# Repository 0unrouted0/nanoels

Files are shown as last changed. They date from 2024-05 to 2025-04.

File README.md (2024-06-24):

This software and instructions are [provided as is](LICENSE), without warranty of any kind.

See [the data of kachurovskiy](https://github.com/kachurovskiy/nanoels/) for the original NanoEls

# NanoEls H4 revised1 (currently unfinished work!!)
* This is an idea of an low cost variant with multiple placement and handsolder types for the components. For e.g.
    * PCB double sided 100mm x 100mm standard type
    * Design with free KiCad 8
    * All parts for hand solder (TCA8418 tricky, but possible - or usage of Adafruit Module)
    * One PCB for keypad and controls
    * Powering over USB or step-down converter with screw terminals
    * Interfacing to LCD via I2C interface over 4 pins possible (== same LCD type with I2C backpack PCB as sold on Aliexpress)
    * USB program and serial interface variants FT232RL or CH340 series
    * USB Connectors 90° types in two sides (idea: back connector>power, front connector>PC-control) or side entry both over 180° Types
    * ESP32-S3-WROOM-1 also possible (with antenna), currently used N16R8

* What's working in Hardware (with modified software)?
	* WARNING: This special hardware version is not checked against EMC, CE, FCC and so on...
    * Display over I2C Interface
    * Programming and serial interface over FT232RL for the ESP32-S3-WROOM-1 (N16R8)
    * Keypad with direct soldered Keypad controller

* What's working in Software?
    * Software should be (i can not test it) compatible with the original NanoEls H4
    * Software working with ardunio Espressive ESP32 3.0.1 boards package (based on ESP-IDF v5.1.4). Maybe NOT backwards compatible to 2.x.
    * Display in I2C mode working. Faultless together with secondary I2C channel for keypad interface. 
    * Added LiquidCrystal_I2C_pt for handling of two I2C interfaces an changeable pins, because there are no available Arduino libraries with I2C pointer parameter.
    * Currently not completely tested, but encoder detects something. Hardware timer for ASYNC and A1 mode maybe not 100% working (unclear).

* ToDo's and current bugs
    * More testing of HW and SW
    * Integration in a real lathe
    * Making a low cost 3d-printable housing
    * PCB: Pitch of buzzer is false for the delivered type. Maybe a dual pitch package is sensible
    * PCB: Through hole pad for thermal connection of ESP32 module should have a bigger size free of solder mask
    * PCB: maybe dual package in standard sizes for buzzer free wheeling diode
    * PCB: upload the latest version

PCB_H4revised1_3d_viewer
PCB_H4revised1_pic1

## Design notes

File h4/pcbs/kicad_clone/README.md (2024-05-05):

- imported easyeda projects directly with KiCad 8.0.2 and saved files
- seems OK, but not tested for importing failures

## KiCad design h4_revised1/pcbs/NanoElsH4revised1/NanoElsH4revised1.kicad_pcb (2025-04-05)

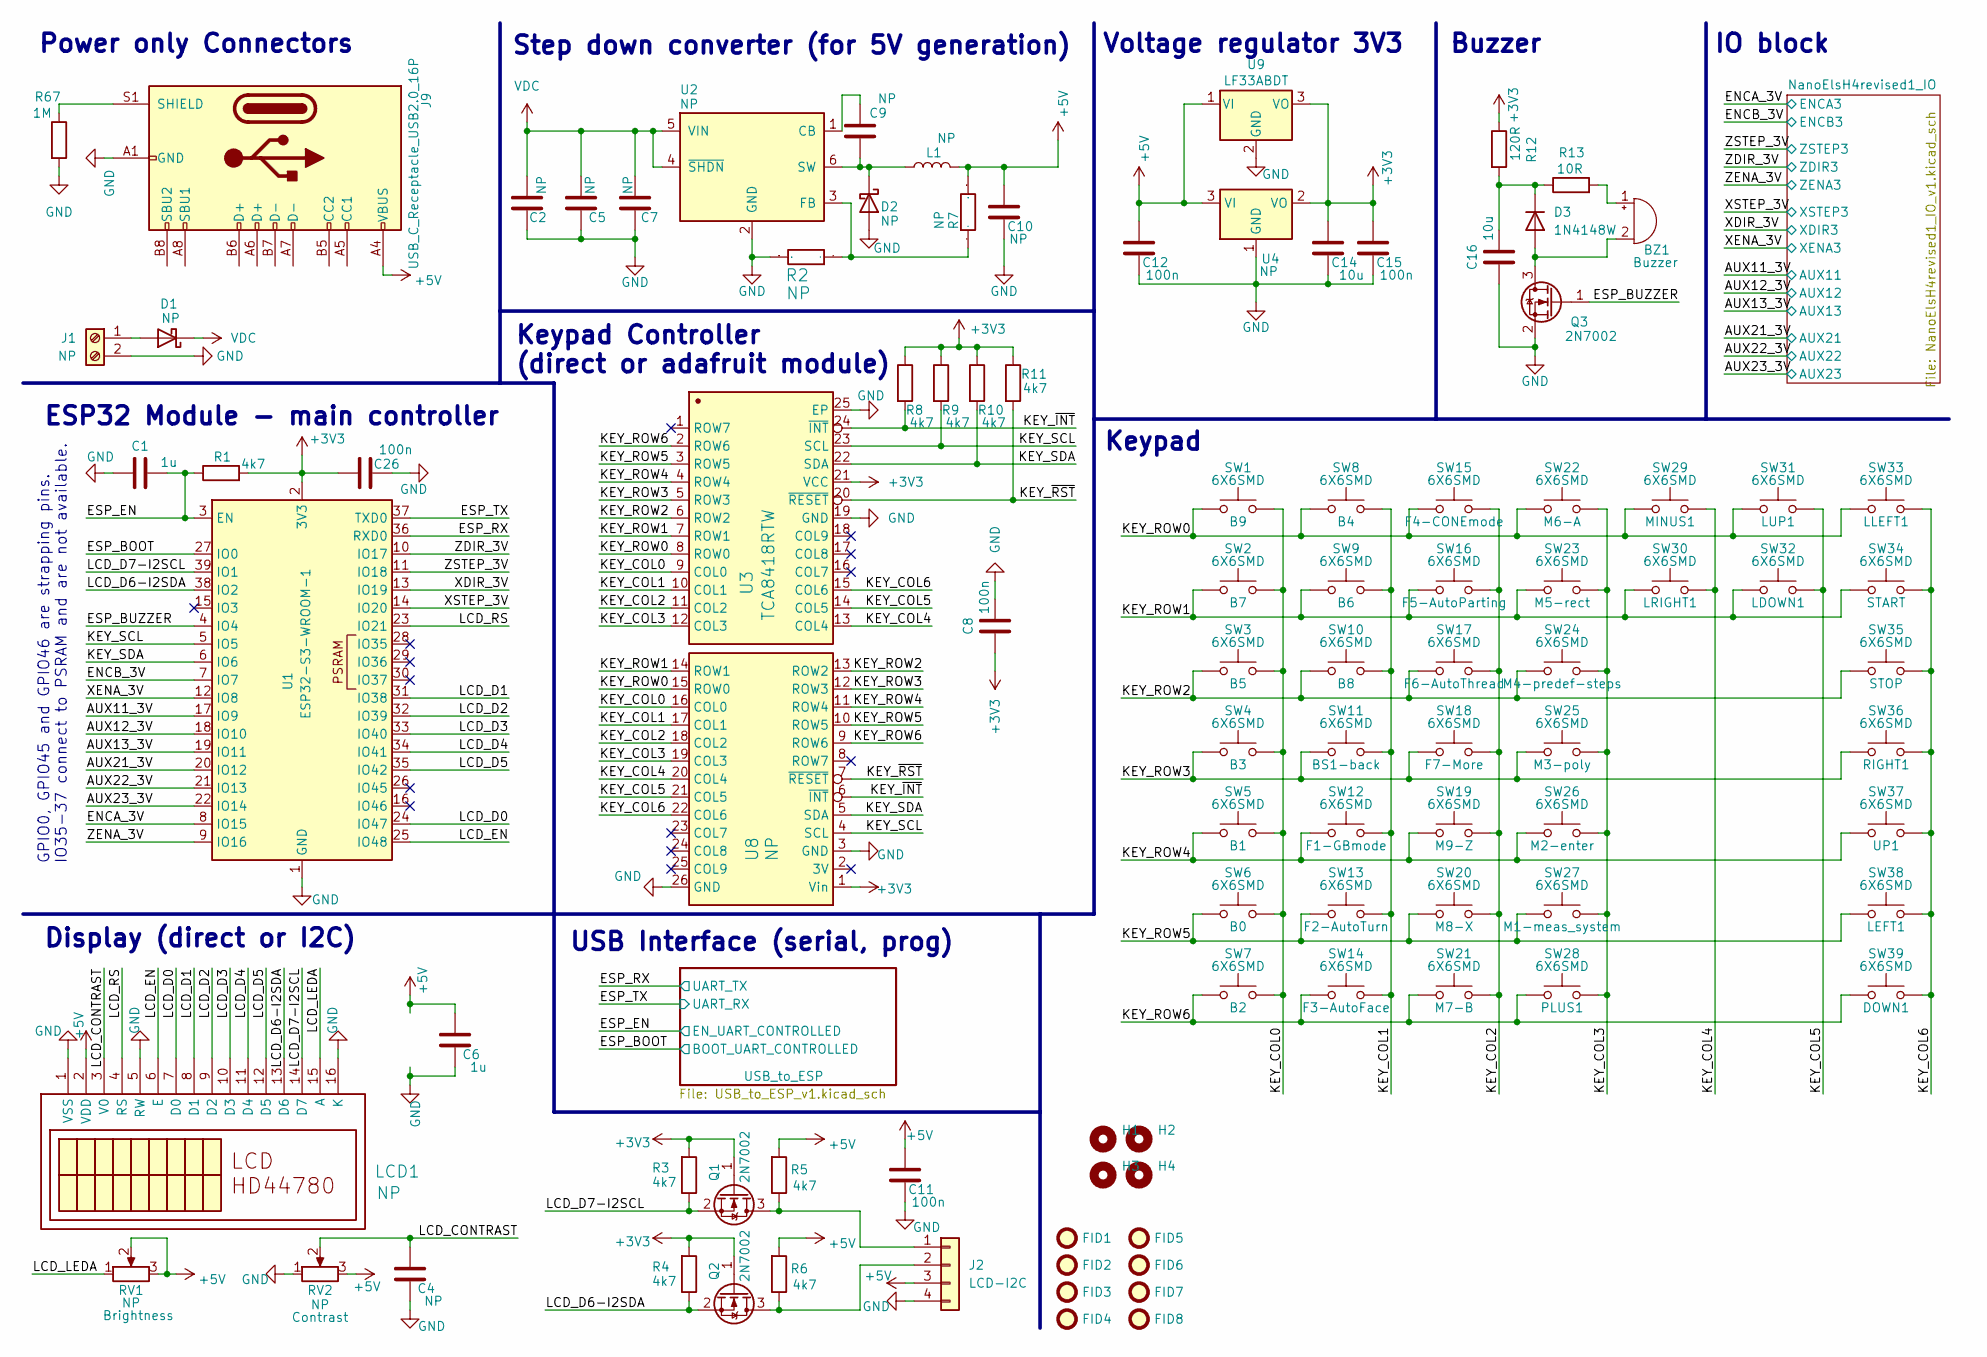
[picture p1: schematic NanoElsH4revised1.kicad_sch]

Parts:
BZ1: Buzzer; MagneticBuzzer_PUI_AT-0927-TT-6-R
C1, C6: 1u; C_0603_1608Metric
C2, C5: NP; C_1210_3225Metric
C4, C7, C9: NP; C_0603_1608Metric
C8, C11, C12, C15, C26: 100n; C_0603_1608Metric
C10: NP; C_1206_3216Metric
C14, C16: 10u; C_1206_3216Metric
D1, D2: NP; D_SMA
D3: 1N4148W; D_SOD-323
FID1, FID2, FID3, FID4, FID5, FID6, FID7, FID8: Fiducial_1.5mm_Mask3mm
H1, H2, H3, H4: MountingHole_3.2mm_M3
J1: NP; PhoenixContact_MCV_1,5_2-G-3.5_1x02_P3.50mm_Vertical
J2: LCD-I2C; PinHeader_1x04_P2.54mm_Horizontal
J9: USB_C_Receptacle_USB2.0_16P; USB_C_HorVert_topbot_GCT-JAE-HRO_USB4160-DX07S024WJ3R400-C3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
L1: NP; L_TDK_VLS6045EX_VLS6045AF
LCD1: NP; LCD_HD44780_header_horizontal
Q1, Q2, Q3: 2N7002; SOT-23
R1, R3, R4, R5, R6, R8, R9, R10, R11: 4k7; R_0603_1608Metric
R2, R7: NP; R_0603_1608Metric
R12: 120R; R_0603_1608Metric
R13: 10R; R_0603_1608Metric
R67: 1M; R_0603_1608Metric
RV1, RV2: NP; Potentiometer_ACP_CA6-VSMD_Vertical
SW1, SW2, SW3, SW4, SW5, SW6, SW7, SW8, SW9, SW10, SW11, SW12, SW13, SW14, SW15, SW16, SW17, SW18, SW19, SW20, SW21, SW22, SW23, SW24, SW25, SW26, SW27, SW28, SW29, SW30, SW31, SW32, SW33, SW34, SW35, SW36, SW37, SW38, SW39: 6X6SMD; SW_Push_1P1T_NO_6x6mm_H9.5mm
U1: ESP32-S3-WROOM-1; ESP32-S3-WROOM-1_bighole
U2: NP; SOT-23-6
U3: TCA8418RTW; WQFN-24-1EP_4x4mm_P0.5mm_EP2.45x2.45mm
U4: NP; SOT-223-3_TabPin2
U8: NP; Adafruit_STEMMA_TCA8418
U9: LF33ABDT; TO-252-2

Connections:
+3V3: C8.1, C14.2, C15.2, C26.2, Q1.1 (G), Q2.1 (G), R1.2, R3.2, R4.2, R8.1, R9.1, R10.1, R11.1, R12.1, U1.2 (3V3), U3.21 (VCC), U4.2 (VO), U8.1 (Vin), U9.3 (VO); also elsewhere on the board
+5V: C6.2, C10.2, C11.2, C12.2, J2.3, J9.A4 (VBUS), J9.A9 (VBUS), J9.B4 (VBUS), J9.B9 (VBUS), L1.2, LCD1.2 (VDD), R5.2, R6.2, R7.1, RV1.2, RV1.3, RV2.3, U4.3 (VI), U9.1 (VI); also elsewhere on the board
/AUX11_3V: U1.17 (IO9); also elsewhere on the board
/AUX12_3V: U1.18 (IO10); also elsewhere on the board
/AUX13_3V: U1.19 (IO11); also elsewhere on the board
/AUX21_3V: U1.20 (IO12); also elsewhere on the board
/AUX22_3V: U1.21 (IO13); also elsewhere on the board
/AUX23_3V: U1.22 (IO14); also elsewhere on the board
/ENCA_3V: U1.8 (IO15); also elsewhere on the board
/ENCB_3V: U1.7 (IO7); also elsewhere on the board
/ESP_BOOT: U1.27 (IO0); also elsewhere on the board
/ESP_BUZZER: Q3.1 (G), U1.4 (IO4)
/ESP_EN: C1.2, R1.1, U1.3 (EN); also elsewhere on the board
/ESP_RX: U1.36 (RXD0); also elsewhere on the board
/ESP_TX: U1.37 (TXD0); also elsewhere on the board
/KEY_COL0: SW1.2, SW2.2, SW3.2, SW4.2, SW5.2, SW6.2, SW7.2, U3.9 (COL0), U8.16 (COL0)
/KEY_COL1: SW8.2, SW9.2, SW10.2, SW11.2, SW12.2, SW13.2, SW14.2, U3.10 (COL1), U8.17 (COL1)
/KEY_COL2: SW15.2, SW16.2, SW17.2, SW18.2, SW19.2, SW20.2, SW21.2, U3.11 (COL2), U8.18 (COL2)
/KEY_COL3: SW22.2, SW23.2, SW24.2, SW25.2, SW26.2, SW27.2, SW28.2, U3.12 (COL3), U8.19 (COL3)
/KEY_COL4: SW29.2, SW30.2, U3.13 (COL4), U8.20 (COL4)
/KEY_COL5: SW31.2, SW32.2, U3.14 (COL5), U8.21 (COL5)
/KEY_COL6: SW33.2, SW34.2, SW35.2, SW36.2, SW37.2, SW38.2, SW39.2, U3.15 (COL6), U8.22 (COL6)
/KEY_ROW0: SW1.1, SW8.1, SW15.1, SW22.1, SW29.1, SW31.1, SW33.1, U3.8 (ROW0), U8.15 (ROW0)
/KEY_ROW1: SW2.1, SW9.1, SW16.1, SW23.1, SW30.1, SW32.1, SW34.1, U3.7 (ROW1), U8.14 (ROW1)
/KEY_ROW2: SW3.1, SW10.1, SW17.1, SW24.1, SW35.1, U3.6 (ROW2), U8.13 (ROW2)
/KEY_ROW3: SW4.1, SW11.1, SW18.1, SW25.1, SW36.1, U3.5 (ROW3), U8.12 (ROW3)
/KEY_ROW4: SW5.1, SW12.1, SW19.1, SW26.1, SW37.1, U3.4 (ROW4), U8.11 (ROW4)
/KEY_ROW5: SW6.1, SW13.1, SW20.1, SW27.1, SW38.1, U3.3 (ROW5), U8.10 (ROW5)
/KEY_ROW6: SW7.1, SW14.1, SW21.1, SW28.1, SW39.1, U3.2 (ROW6), U8.9 (ROW6)
/KEY_SCL: R9.2, U1.5 (IO5), U3.23 (SCL), U8.4 (SCL)
/KEY_SDA: R10.2, U1.6 (IO6), U3.22 (SDA), U8.5 (SDA)
/KEY_~INT: R8.2, U3.24 (~INT), U8.6 (~INT)
/KEY_~RST: R11.2, U3.20 (~RESET), U8.7 (~RESET)
/LCD_CONTRAST: C4.2, LCD1.3 (V0), RV2.2
/LCD_D0: LCD1.7 (D0), U1.24 (IO47)
/LCD_D1: LCD1.8 (D1), U1.31 (IO38)
/LCD_D2: LCD1.9 (D2), U1.32 (IO39)
/LCD_D3: LCD1.10 (D3), U1.33 (IO40)
/LCD_D4: LCD1.11 (D4), U1.34 (IO41)
/LCD_D5: LCD1.12 (D5), U1.35 (IO42)
/LCD_D6-I2SDA: LCD1.13 (D6), Q2.2 (S), R4.1, U1.38 (IO2)
/LCD_D7-I2SCL: LCD1.14 (D7), Q1.2 (S), R3.1, U1.39 (IO1)
/LCD_EN: LCD1.6 (E), U1.25 (IO48)
/LCD_LEDA: LCD1.15 (A), RV1.1
/LCD_RS: LCD1.4 (RS), U1.23 (IO21)
/XDIR_3V: U1.13 (IO19); also elsewhere on the board
/XENA_3V: U1.12 (IO8); also elsewhere on the board
/XSTEP_3V: U1.14 (IO20); also elsewhere on the board
/ZDIR_3V: U1.10 (IO17); also elsewhere on the board
/ZENA_3V: U1.9 (IO16); also elsewhere on the board
/ZSTEP_3V: U1.11 (IO18); also elsewhere on the board
GND: C1.1, C2.1, C4.1, C5.1, C6.1, C7.1, C8.2, C10.1, C11.1, C12.1, C14.1, C15.1, C16.1, C26.1, D2.2 (A), J1.2, J2.4, J9.A1 (GND), J9.A12 (GND), J9.B1 (GND), J9.B12 (GND), LCD1.1 (VSS), LCD1.5 (RW), LCD1.16 (K), Q3.2 (S), R2.1, R67.2, RV2.1, U1.1 (GND), U1.40 (GND), U1.41 (GND), U2.2 (GND), U3.19 (GND), U3.25 (EP), U4.1 (GND), U8.3 (GND), U8.26 (GND), U9.2 (GND); also elsewhere on the board
unnamed: BZ1.1 (+), R13.2
unnamed: BZ1.2 (-), D3.2 (A), Q3.3 (D)
unnamed: D1.2 (A), J1.1
unnamed: C9.1, D2.1 (K), L1.1, U2.6 (SW)
unnamed: C16.2, D3.1 (K), R12.2, R13.1
unnamed: J2.1, Q1.3 (D), R5.1
unnamed: J2.2, Q2.3 (D), R6.1
unnamed: J9.S1 (SHIELD), R67.1
unnamed: C9.2, U2.1 (CB)
unnamed: R2.2, R7.2, U2.3 (FB)
VDC: C2.2, C5.2, C7.2, D1.1 (K), U2.4 (~SHDN), U2.5 (VIN)

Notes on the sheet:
USB Interface (serial, prog)
Step down converter (for 5V generation)
Keypad Controller (direct or adafruit module)
GPIO0, GPIO45 and GPIO46 are strapping pins. IO35-37 connect to PSRAM and are not available.
Keypad
ESP32 Module - main controller
Power only Connectors
Buzzer
Display (direct or I2C)
Voltage regulator 3V3
IO block

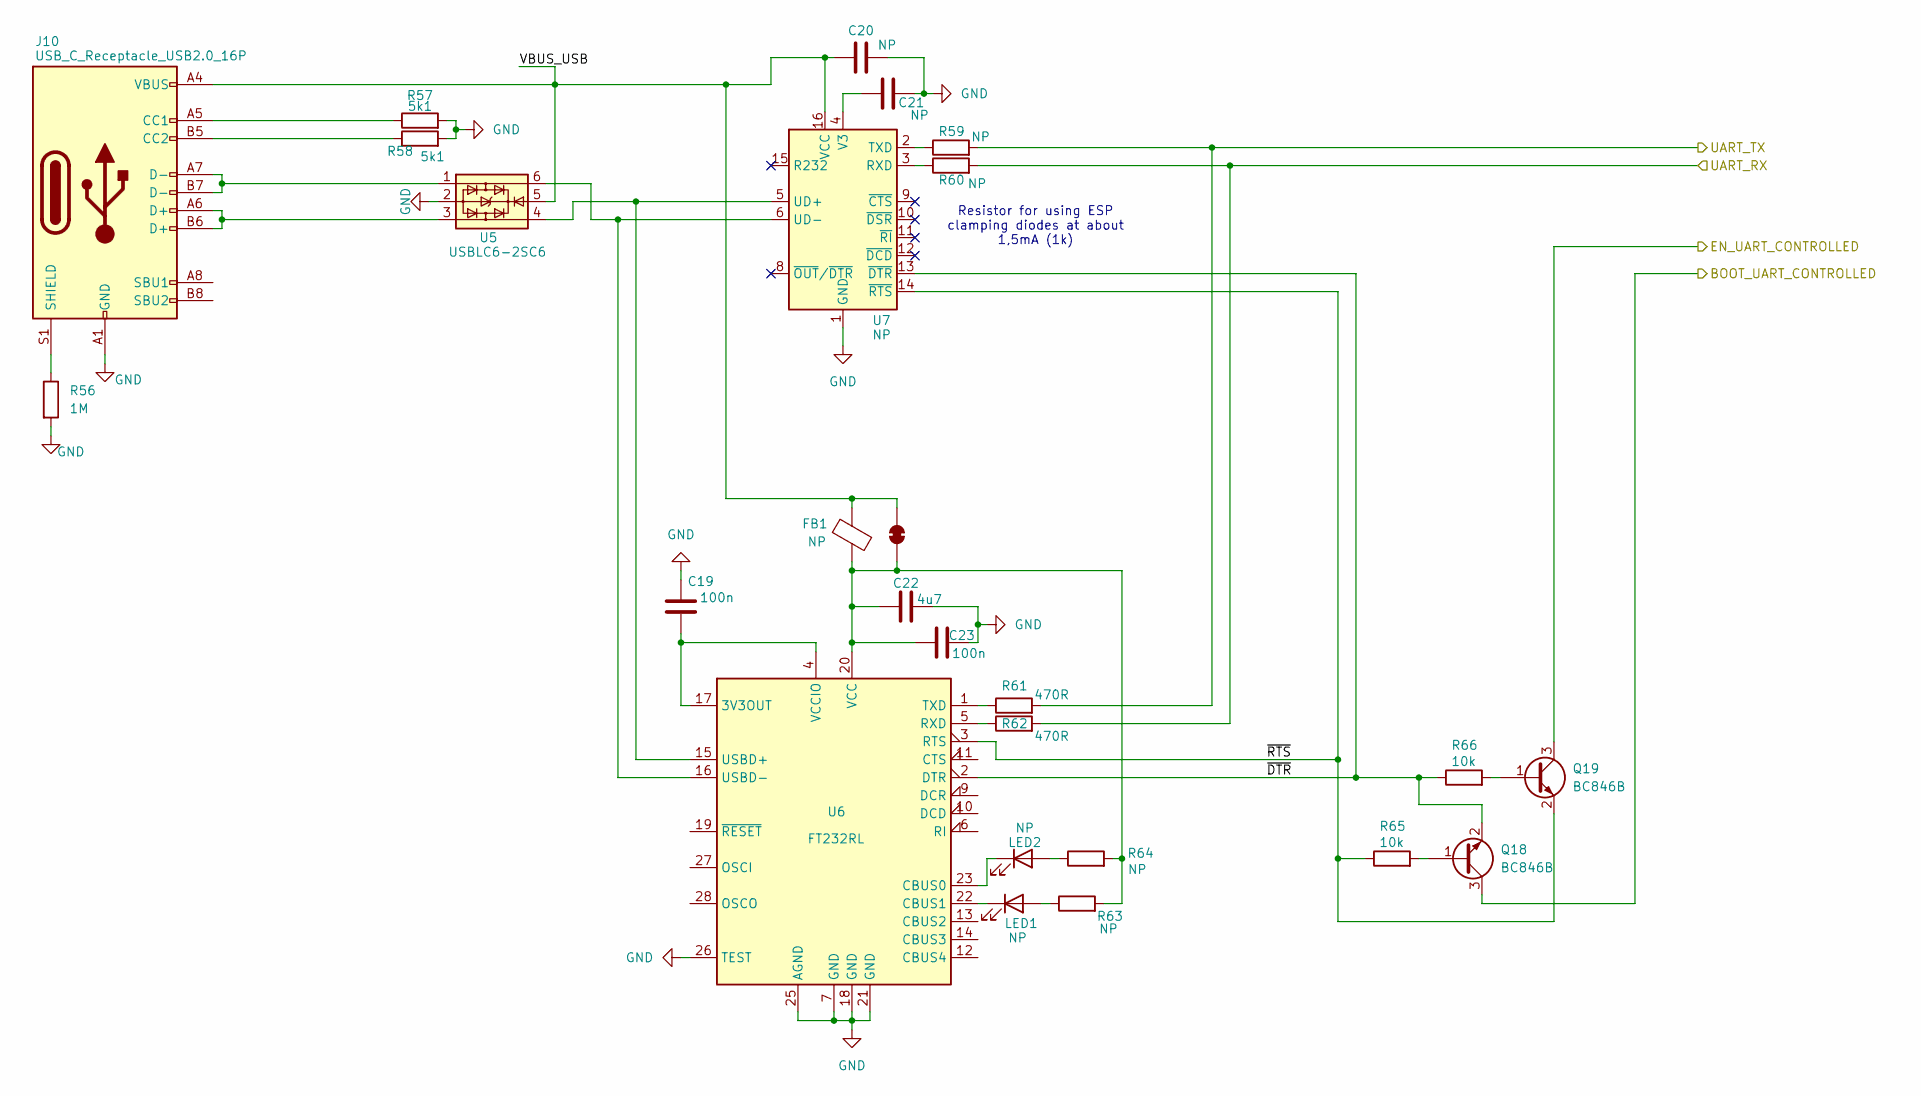
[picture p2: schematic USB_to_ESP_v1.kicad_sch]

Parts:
C19, C23: 100n; C_0603_1608Metric
C20, C21: NP; C_0603_1608Metric
C22: 4u7; C_1206_3216Metric
FB1: NP; L_0603_1608Metric
J10: USB_C_Receptacle_USB2.0_16P; USB_C_HorVert_top_GCT-JAE-HRO_USB4160-DX07S024WJ3R400-C31M12
JP1: R_0603_1608Metric_shorted
LED1, LED2: NP; LED_0603_1608Metric
Q18, Q19: BC846B; SOT-23
R56: 1M; R_0603_1608Metric
R57, R58: 5k1; R_0603_1608Metric
R59, R60, R63, R64: NP; R_0603_1608Metric
R61, R62: 470R; R_0603_1608Metric
R65, R66: 10k; R_0603_1608Metric
U5: USBLC6-2SC6; SOT-23-6
U6: FT232RL; SSOP-28_5.3x10.2mm_P0.65mm
U7: NP; SOIC-16_3.9x9.9mm_P1.27mm

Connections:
/ESP_BOOT: Q18.3 (C); also elsewhere on the board
/ESP_EN: Q19.3 (C); also elsewhere on the board
/ESP_RX: R59.2, R61.2; also elsewhere on the board
/ESP_TX: R60.2, R62.2; also elsewhere on the board
/USB_to_ESP/VBUS_USB: C20.1, FB1.2, J10.A4 (VBUS), J10.A9 (VBUS), J10.B4 (VBUS), J10.B9 (VBUS), JP1.2 (B), U5.5, U7.16 (VCC)
/USB_to_ESP/~DTR: Q18.2 (E), R66.1, U6.2 (DTR), U7.13 (~DTR)
/USB_to_ESP/~RTS: Q19.2 (E), R65.1, U6.3 (RTS), U7.14 (~RTS)
GND: C19.2, C20.2, C21.2, C22.1, C23.1, J10.A1 (GND), J10.A12 (GND), J10.B1 (GND), J10.B12 (GND), R56.2, R57.2, R58.2, U5.2, U6.7 (GND), U6.18 (GND), U6.21 (GND), U6.25 (AGND), U6.26 (TEST), U7.1 (GND); also elsewhere on the board
unnamed: J10.A5 (CC1), R57.1
unnamed: J10.B5 (CC2), R58.1
unnamed: J10.A6 (D+), J10.B6 (D+), U5.3
unnamed: J10.A7 (D-), J10.B7 (D-), U5.1
unnamed: J10.S1 (SHIELD), R56.1
unnamed: C22.2, C23.2, FB1.1, JP1.1 (A), R63.2, R64.2, U6.20 (VCC)
unnamed: LED1.2 (A), R63.1
unnamed: LED1.1 (K), U6.22 (CBUS1)
unnamed: LED2.2 (A), R64.1
unnamed: LED2.1 (K), U6.23 (CBUS0)
unnamed: Q18.1 (B), R65.2
unnamed: Q19.1 (B), R66.2
unnamed: C19.1, U6.4 (VCCIO), U6.17 (3V3OUT)
unnamed: R62.1, U6.5 (RXD)
unnamed: R61.1, U6.1 (TXD)
unnamed: U5.4, U6.15 (USBD+), U7.5 (UD+)
unnamed: U5.6, U6.16 (USBD-), U7.6 (UD-)
unnamed: R60.1, U7.3 (RXD)
unnamed: R59.1, U7.2 (TXD)
unnamed: C21.1, U7.4 (V3)

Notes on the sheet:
Resistor for using ESP clamping diodes at about 1,5mA (1k)

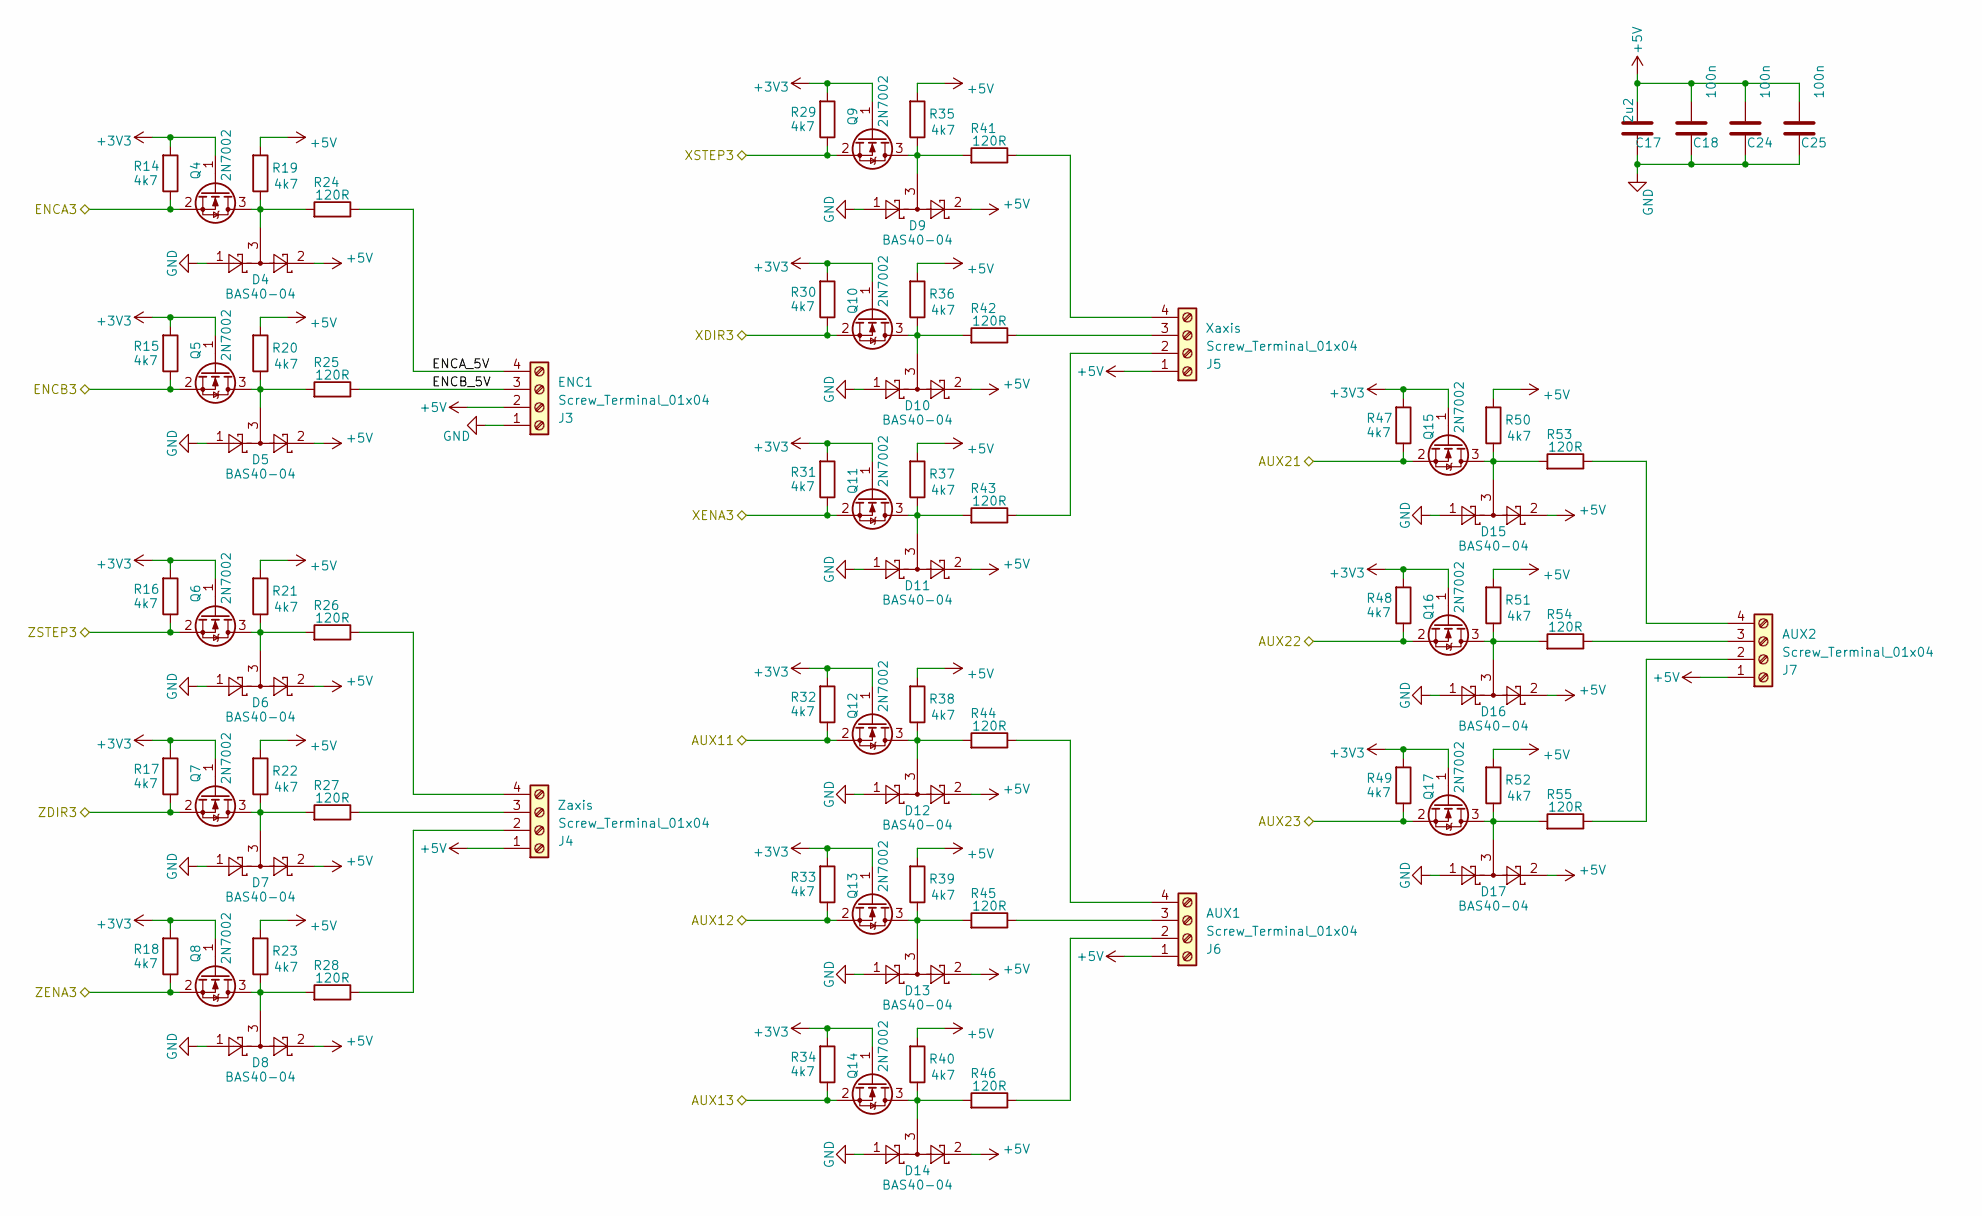
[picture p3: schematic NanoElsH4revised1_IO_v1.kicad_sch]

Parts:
C17: 2u2; C_1206_3216Metric
C18, C24, C25: 100n; C_0603_1608Metric
D4, D5, D6, D7, D8, D9, D10, D11, D12, D13, D14, D15, D16, D17: BAS40-04; SOT-23
J3, J4, J5, J6, J7: Screw_Terminal_01x04; PhoenixContact_MCV_1,5_4-G-3.5_1x04_P3.50mm_Vertical
Q4, Q5, Q6, Q7, Q8, Q9, Q10, Q11, Q12, Q13, Q14, Q15, Q16, Q17: 2N7002; SOT-23
R14, R15, R16, R17, R18, R19, R20, R21, R22, R23, R29, R30, R31, R32, R33, R34, R35, R36, R37, R38, R39, R40, R47, R48, R49, R50, R51, R52: 4k7; R_0603_1608Metric
R24, R25, R26, R27, R28, R41, R42, R43, R44, R45, R46, R53, R54, R55: 120R; R_0603_1608Metric

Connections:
+3V3: Q4.1 (G), Q5.1 (G), Q6.1 (G), Q7.1 (G), Q8.1 (G), Q9.1 (G), Q10.1 (G), Q11.1 (G), Q12.1 (G), Q13.1 (G), Q14.1 (G), Q15.1 (G), Q16.1 (G), Q17.1 (G), R14.2, R15.2, R16.2, R17.2, R18.2, R29.2, R30.2, R31.2, R32.2, R33.2, R34.2, R47.2, R48.2, R49.2; also elsewhere on the board
+5V: C17.2, C18.2, C24.2, C25.2, D4.2, D5.2, D6.2, D7.2, D8.2, D9.2, D10.2, D11.2, D12.2, D13.2, D14.2, D15.2, D16.2, D17.2, J3.2, J4.1, J5.1, J6.1, J7.1, R19.2, R20.2, R21.2, R22.2, R23.2, R35.2, R36.2, R37.2, R38.2, R39.2, R40.2, R50.2, R51.2, R52.2; also elsewhere on the board
/AUX11_3V: Q12.2 (S), R32.1; also elsewhere on the board
/AUX12_3V: Q13.2 (S), R33.1; also elsewhere on the board
/AUX13_3V: Q14.2 (S), R34.1; also elsewhere on the board
/AUX21_3V: Q15.2 (S), R47.1; also elsewhere on the board
/AUX22_3V: Q16.2 (S), R48.1; also elsewhere on the board
/AUX23_3V: Q17.2 (S), R49.1; also elsewhere on the board
/ENCA_3V: Q4.2 (S), R14.1; also elsewhere on the board
/ENCB_3V: Q5.2 (S), R15.1; also elsewhere on the board
/NanoElsH4revised1_IO/ENCA_5V: J3.4, R24.1
/NanoElsH4revised1_IO/ENCB_5V: J3.3, R25.1
/XDIR_3V: Q10.2 (S), R30.1; also elsewhere on the board
/XENA_3V: Q11.2 (S), R31.1; also elsewhere on the board
/XSTEP_3V: Q9.2 (S), R29.1; also elsewhere on the board
/ZDIR_3V: Q7.2 (S), R17.1; also elsewhere on the board
/ZENA_3V: Q8.2 (S), R18.1; also elsewhere on the board
/ZSTEP_3V: Q6.2 (S), R16.1; also elsewhere on the board
GND: C17.1, C18.1, C24.1, C25.1, D4.1, D5.1, D6.1, D7.1, D8.1, D9.1, D10.1, D11.1, D12.1, D13.1, D14.1, D15.1, D16.1, D17.1, J3.1; also elsewhere on the board
unnamed: J4.2, R28.1
unnamed: J4.3, R27.1
unnamed: J4.4, R26.1
unnamed: J5.2, R43.1
unnamed: J5.3, R42.1
unnamed: J5.4, R41.1
unnamed: J6.2, R46.1
unnamed: J6.3, R45.1
unnamed: J6.4, R44.1
unnamed: J7.2, R55.1
unnamed: J7.3, R54.1
unnamed: J7.4, R53.1
unnamed: D4.3, Q4.3 (D), R19.1, R24.2
unnamed: D5.3, Q5.3 (D), R20.1, R25.2
unnamed: D6.3, Q6.3 (D), R21.1, R26.2
unnamed: D7.3, Q7.3 (D), R22.1, R27.2
unnamed: D8.3, Q8.3 (D), R23.1, R28.2
unnamed: D9.3, Q9.3 (D), R35.1, R41.2
unnamed: D10.3, Q10.3 (D), R36.1, R42.2
unnamed: D11.3, Q11.3 (D), R37.1, R43.2
unnamed: D12.3, Q12.3 (D), R38.1, R44.2
unnamed: D13.3, Q13.3 (D), R39.1, R45.2
unnamed: D14.3, Q14.3 (D), R40.1, R46.2
unnamed: D15.3, Q15.3 (D), R50.1, R53.2
unnamed: D16.3, Q16.3 (D), R51.1, R54.2
unnamed: D17.3, Q17.3 (D), R52.1, R55.2

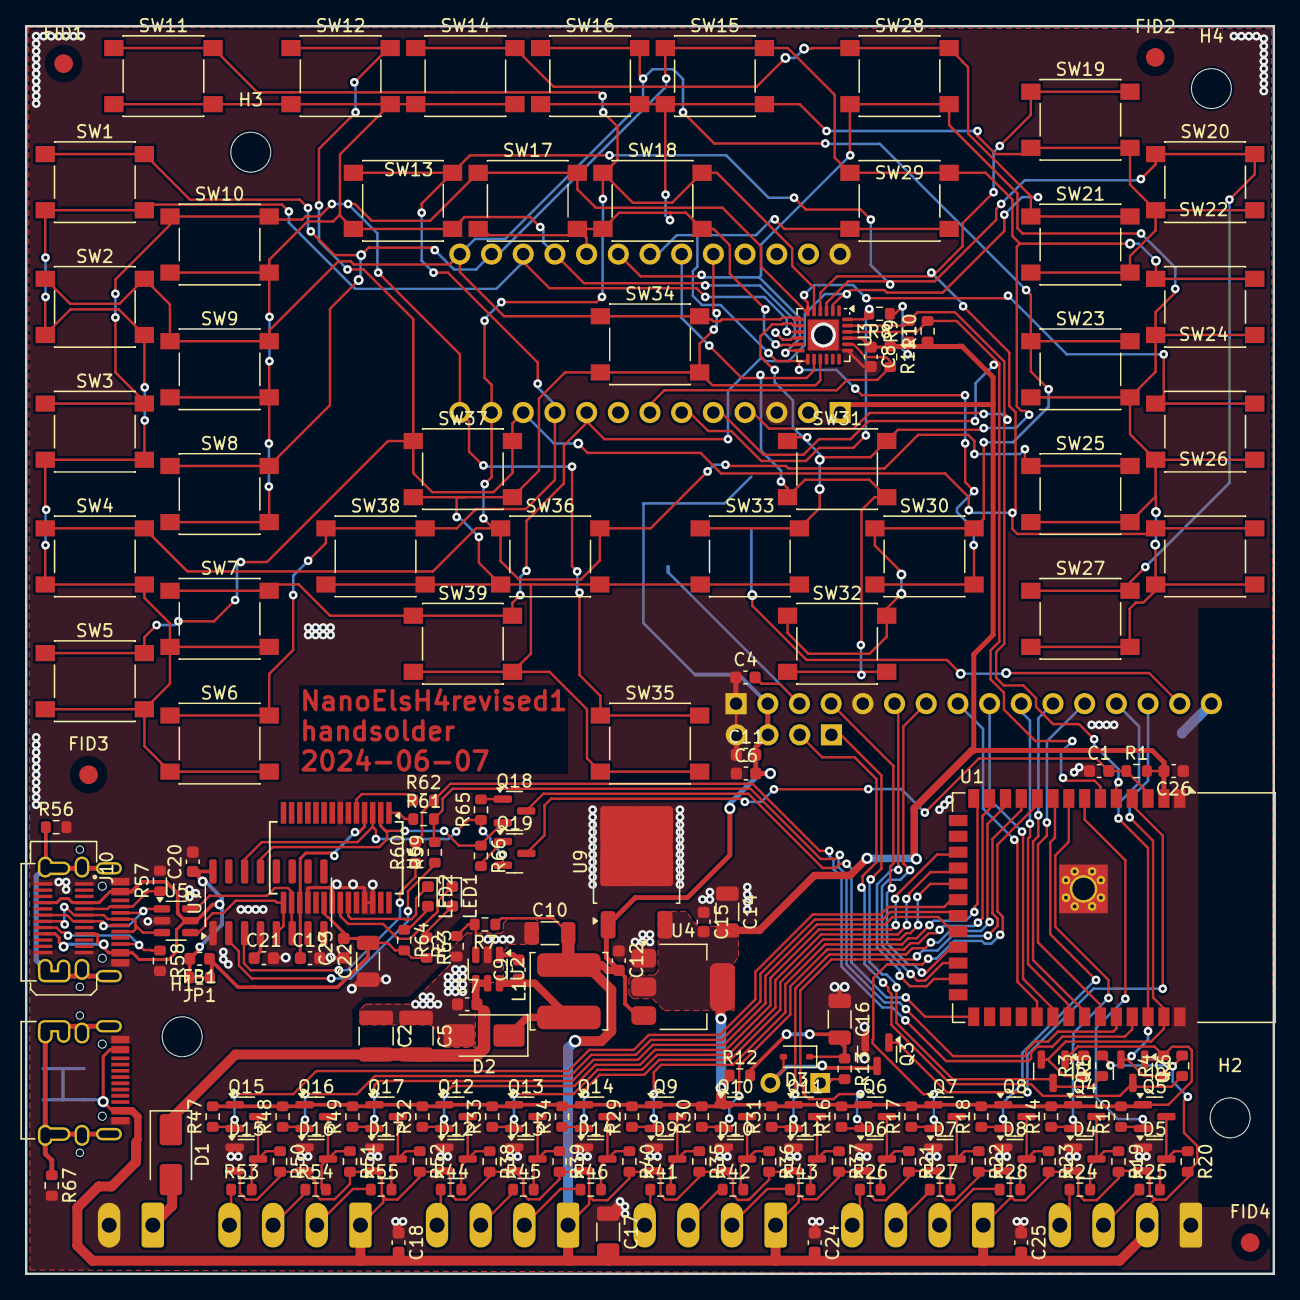
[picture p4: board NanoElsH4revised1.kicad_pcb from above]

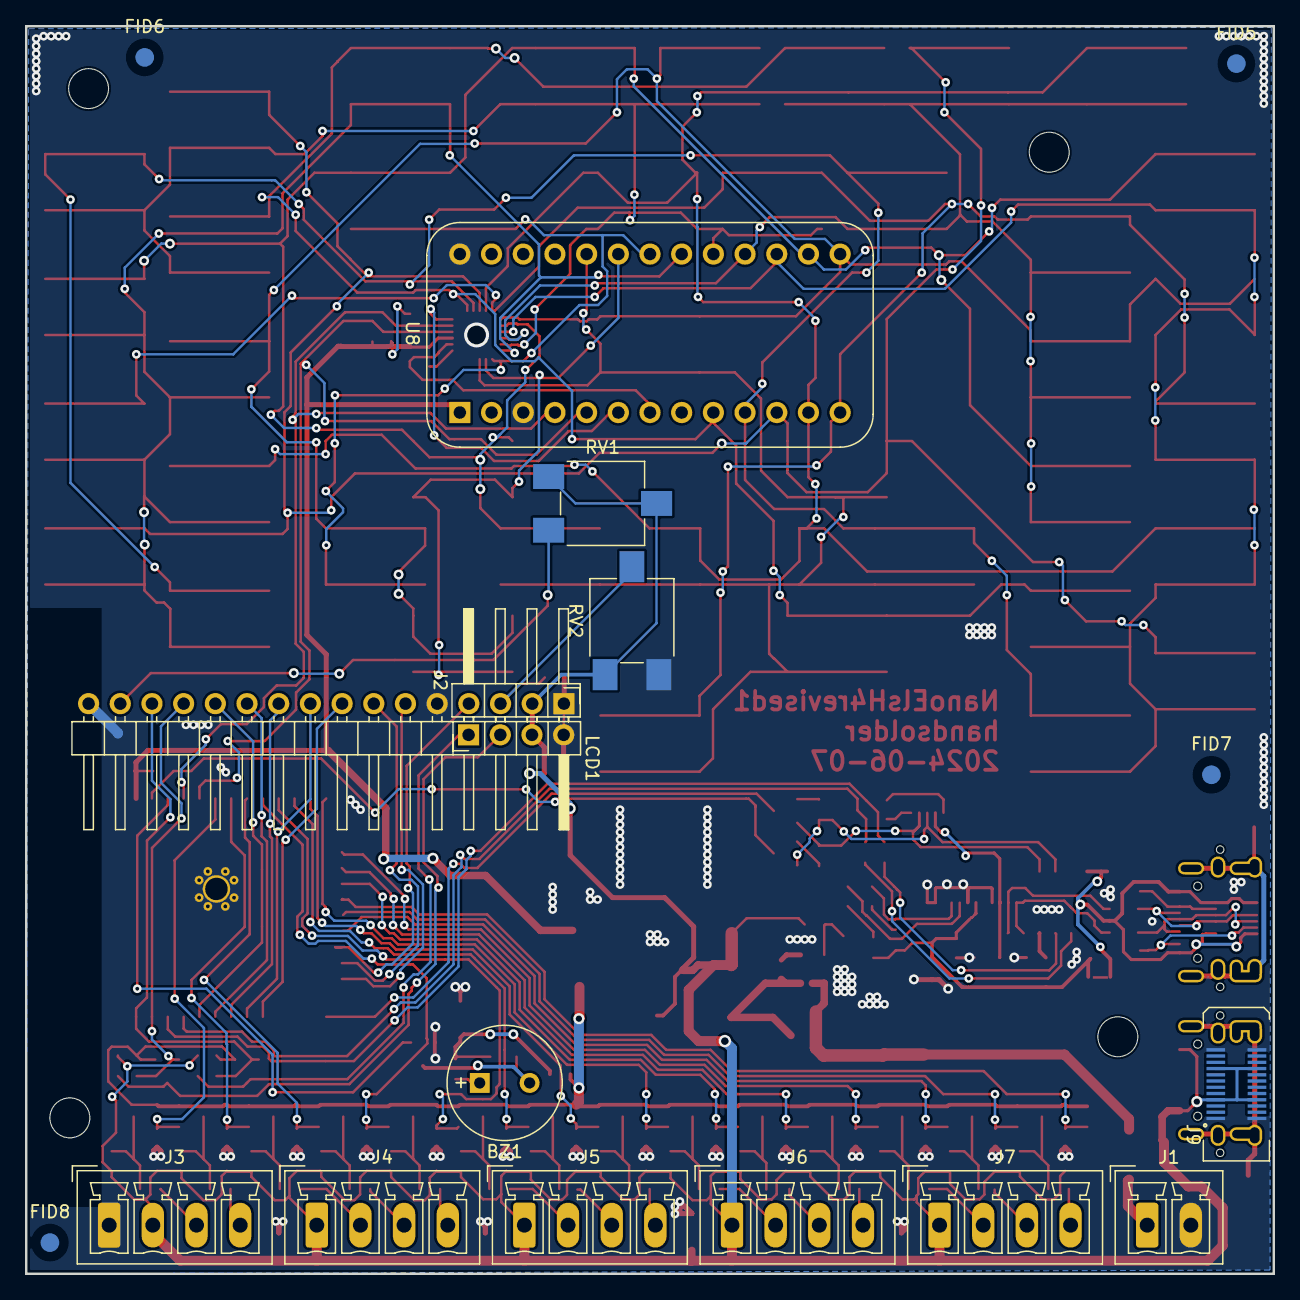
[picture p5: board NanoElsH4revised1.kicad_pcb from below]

Board: 2 copper layers, 100.0 x 100.0 mm, 205 parts (17 on the bottom side), 114 nets.

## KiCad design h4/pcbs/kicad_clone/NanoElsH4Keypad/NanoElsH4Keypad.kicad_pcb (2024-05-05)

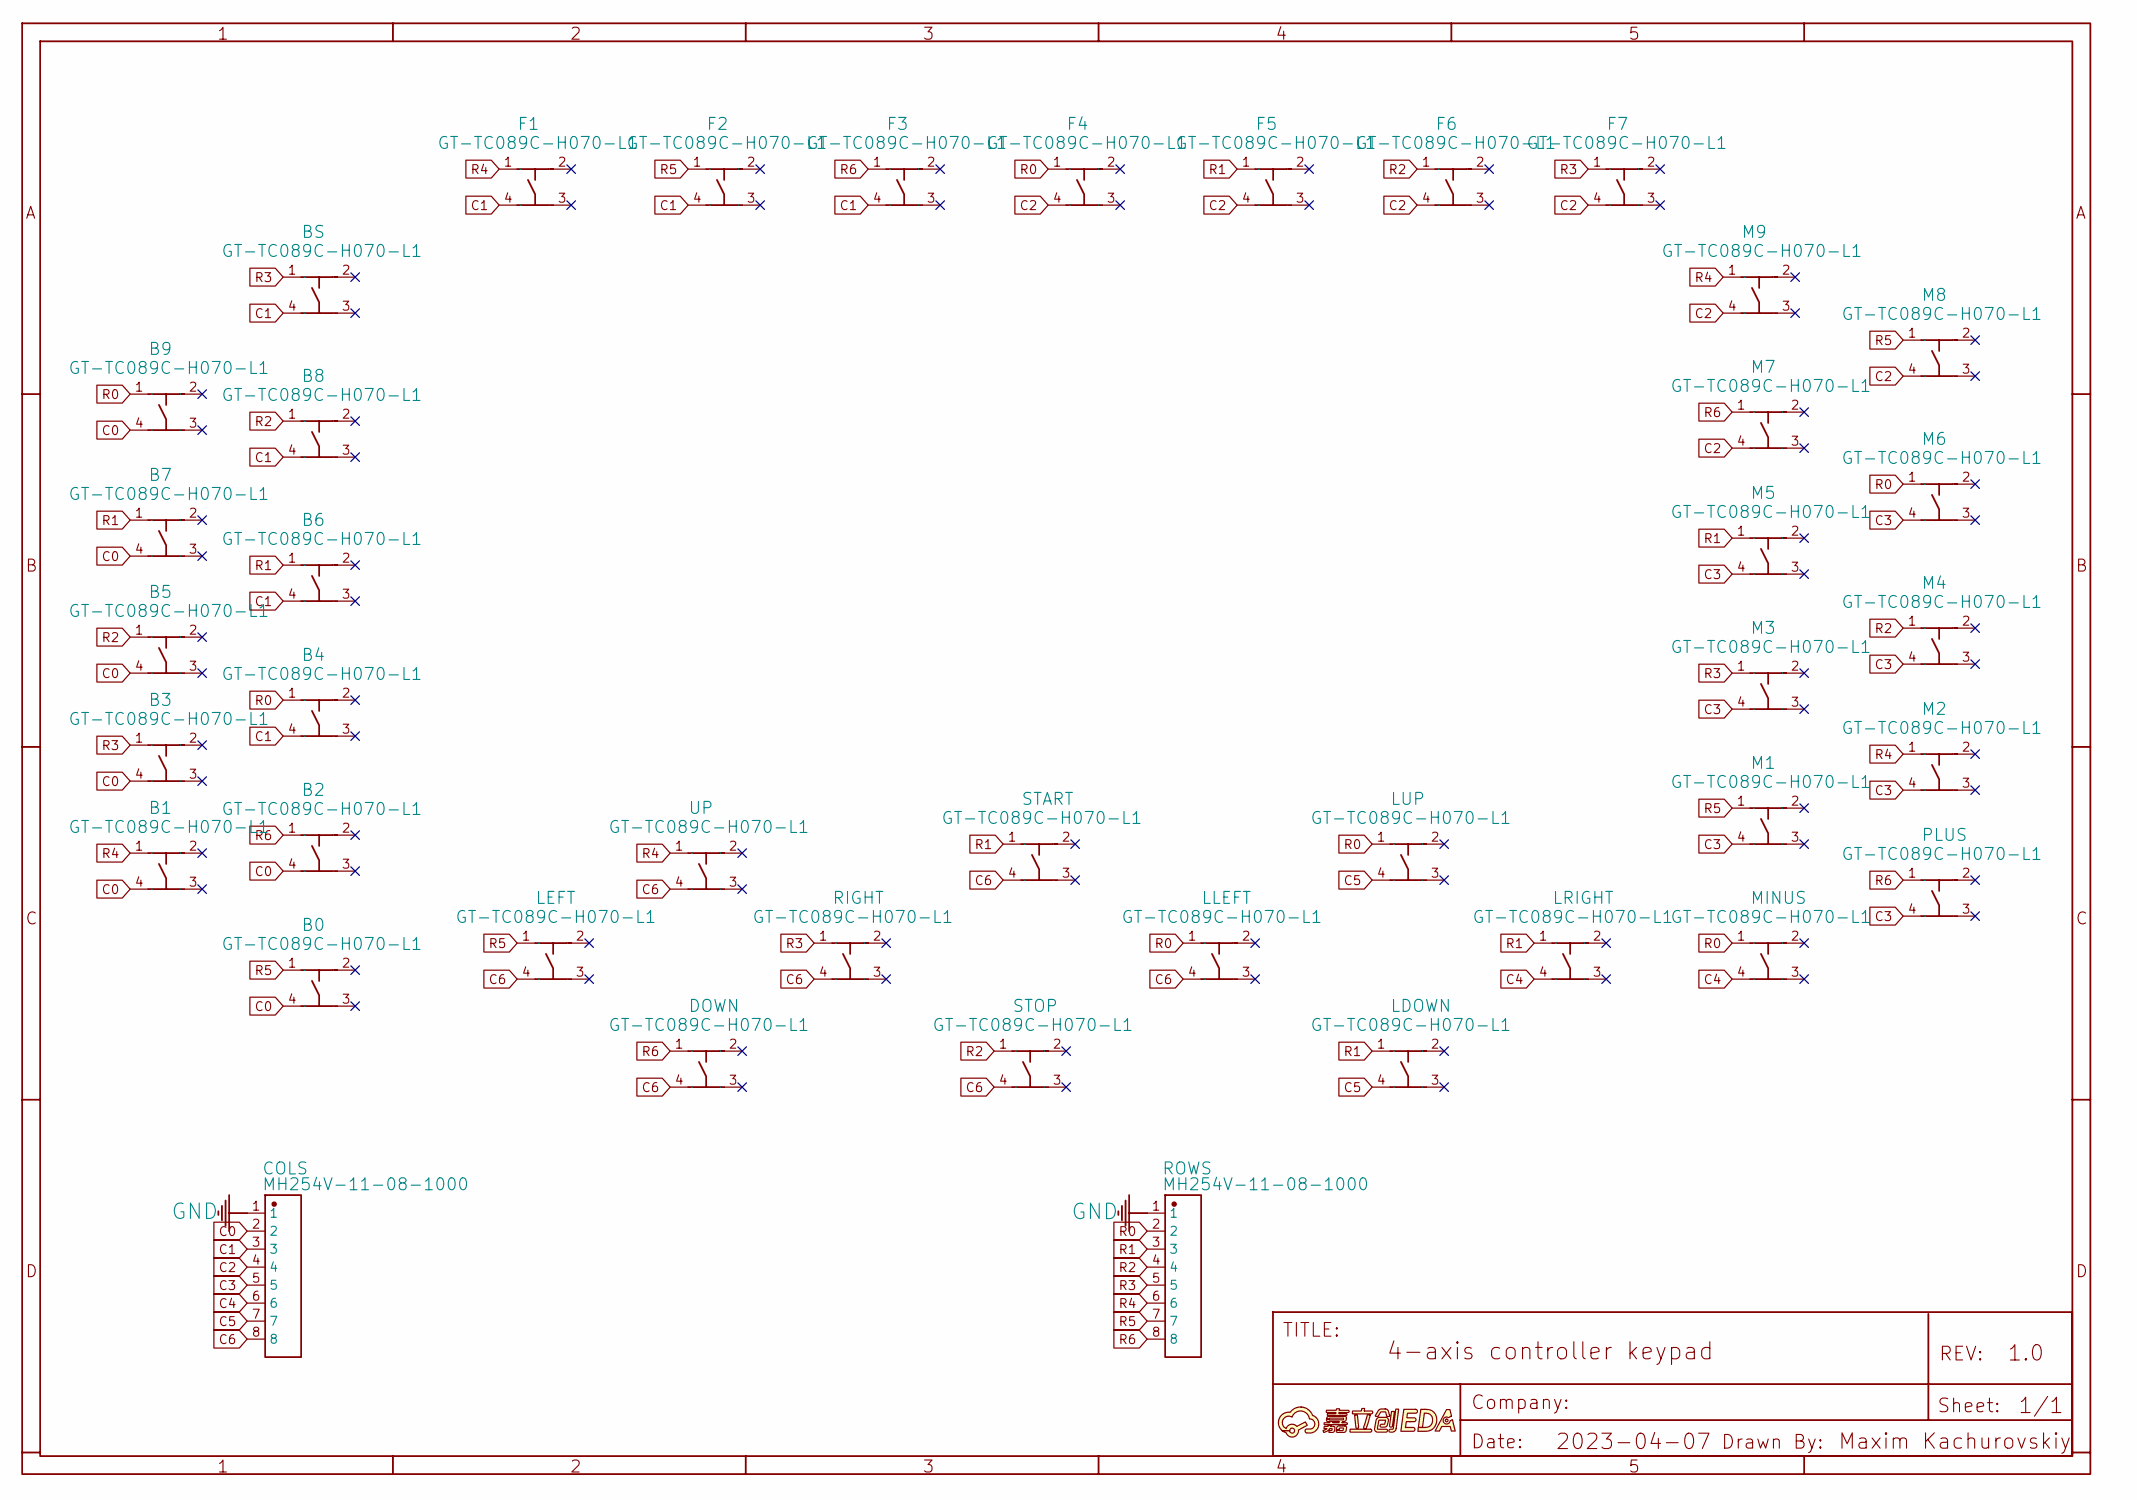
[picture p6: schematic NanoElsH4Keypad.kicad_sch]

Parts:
A: A
B0, B1, B2, B3, B4, B5, B6, B7, B8, B9: GT-TC089C-H070-L1
BS: GT-TC089C-H070-L1
COLS: MH254V-11-08-1000
DOWN: GT-TC089C-H070-L1
F1, F2, F3, F4, F5, F6, F7: GT-TC089C-H070-L1
LDOWN: GT-TC089C-H070-L1
LEFT: GT-TC089C-H070-L1
LLEFT: GT-TC089C-H070-L1
LRIGHT: GT-TC089C-H070-L1
LUP: GT-TC089C-H070-L1
M1, M2, M3, M4, M5, M6, M7, M8, M9: GT-TC089C-H070-L1
MINUS: GT-TC089C-H070-L1
PLUS: GT-TC089C-H070-L1
RIGHT: GT-TC089C-H070-L1
ROWS: MH254V-11-08-1000
START: GT-TC089C-H070-L1
STOP: GT-TC089C-H070-L1
UP: GT-TC089C-H070-L1

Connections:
C0: B0.4, B1.4, B2.4, B3.4, B5.4, B7.4, B9.4, COLS.2
C1: B4.4, B6.4, B8.4, BS.4, COLS.3, F1.4, F2.4, F3.4
C2: COLS.4, F4.4, F5.4, F6.4, F7.4, M7.4, M8.4, M9.4
C3: COLS.5, M1.4, M2.4, M3.4, M4.4, M5.4, M6.4, PLUS.4
C4: COLS.6, LRIGHT.4, MINUS.4
C5: COLS.7, LDOWN.4, LUP.4
C6: COLS.8, DOWN.4, LEFT.4, LLEFT.4, RIGHT.4, START.4, STOP.4, UP.4
GND: COLS.1, ROWS.1
R0: B4.1, B9.1, F4.1, LLEFT.1, LUP.1, M6.1, MINUS.1, ROWS.2
R1: B6.1, B7.1, F5.1, LDOWN.1, LRIGHT.1, M5.1, ROWS.3, START.1
R2: B5.1, B8.1, F6.1, M4.1, ROWS.4, STOP.1
R3: B3.1, BS.1, F7.1, M3.1, RIGHT.1, ROWS.5
R4: B1.1, F1.1, M2.1, M9.1, ROWS.6, UP.1
R5: B0.1, F2.1, LEFT.1, M1.1, M8.1, ROWS.7
R6: B2.1, DOWN.1, F3.1, M7.1, PLUS.1, ROWS.8

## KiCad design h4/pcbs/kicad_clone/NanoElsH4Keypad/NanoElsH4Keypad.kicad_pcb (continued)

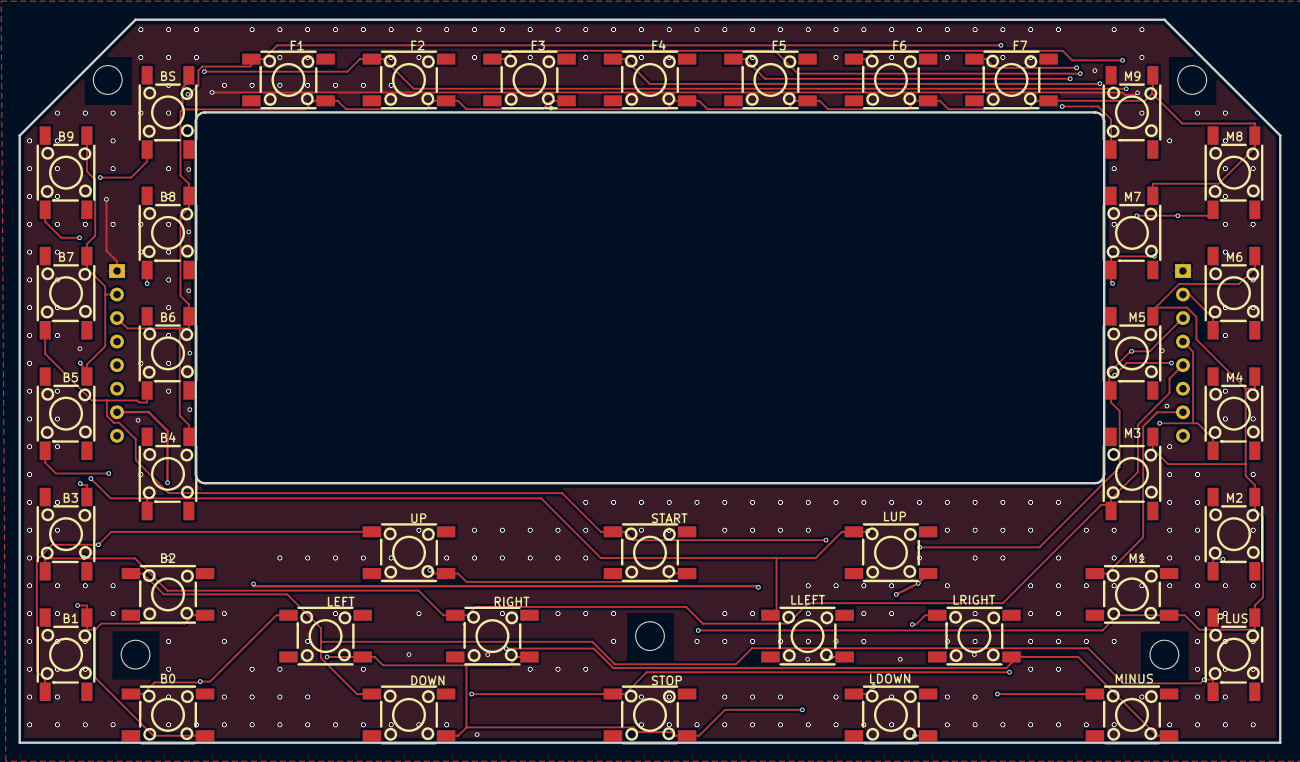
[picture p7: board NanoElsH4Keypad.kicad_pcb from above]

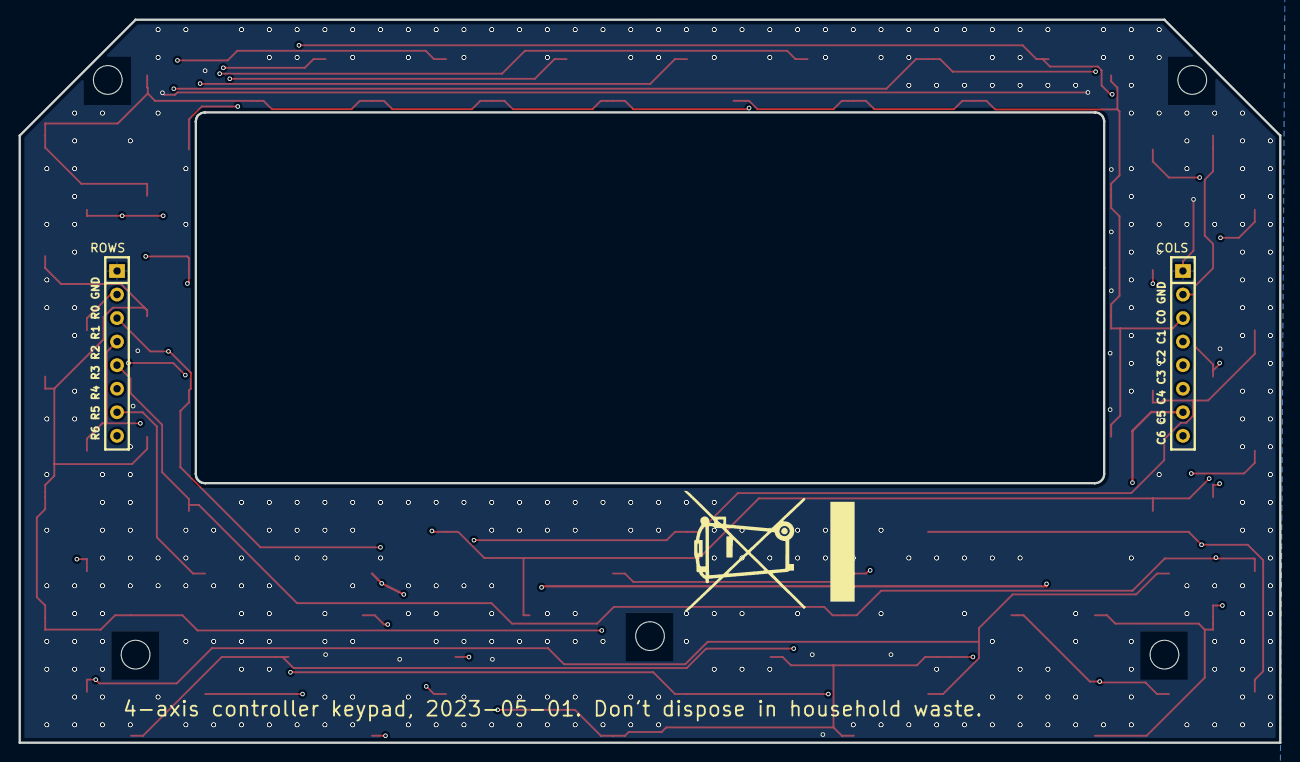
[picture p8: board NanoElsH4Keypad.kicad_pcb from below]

Board: 4 copper layers, 136.0 x 78.0 mm, 46 parts (2 on the bottom side), 15 nets.

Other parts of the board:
Hole_gge12452: Hole_gge12452
Hole_gge12497: Hole_gge12497
Hole_gge12557: Hole_gge12557
Hole_gge12572: Hole_gge12572
Hole_gge12587: Hole_gge12587

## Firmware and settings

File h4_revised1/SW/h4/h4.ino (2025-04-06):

// https://github.com/kachurovskiy/nanoels

/* Change values in this section to suit your hardware. */

#define DISPLAY_I2C_EXPANDER /* Define this for using an Display with I2C expander board */

// Define your hardware parameters here.
const int ENCODER_PPR = 600; // 600 step spindle optical rotary encoder. Fractional values not supported.
const int ENCODER_BACKLASH = 3; // Numer of impulses encoder can issue without movement of the spindle

// Spindle rotary encoder pins. Swap values if the rotation direction is wrong.
#define ENC_A 7
#define ENC_B 15

// Main lead screw (Z) parameters.
const long SCREW_Z_DU = 20000; // 2mm lead screw in deci-microns (10^-7 of a meter)
const long MOTOR_STEPS_Z = 800;
const long SPEED_START_Z = 1200; // Initial speed of a motor, steps / second.
const long ACCELERATION_Z = 20 * MOTOR_STEPS_Z; // Acceleration of a motor, steps / second ^ 2.
const long SPEED_MANUAL_MOVE_Z = 6 * MOTOR_STEPS_Z; // Maximum speed of a motor during manual move, steps / second.
const bool INVERT_Z = false; // change (true/false) if the carriage moves e.g. "left" when you press "right".
const bool NEEDS_REST_Z = false; // Set to false for closed-loop drivers, true for open-loop.
const long MAX_TRAVEL_MM_Z = 500; // Lathe bed doesn't allow to travel more than this in one go, 50cm
//const long BACKLASH_DU_Z = 4000; // 0.40mm backlash in deci-microns (10^-7 of a meter)
const char NAME_Z = 'Z'; // Text shown on screen before axis position value, GCode axis name

// Cross-slide lead screw (X) parameters.
const long SCREW_X_DU = 20000; // 2mm lead screw in deci-microns (10^-7) of a meter
const long MOTOR_STEPS_X = 2400; // 800 steps at 3x reduction
const long SPEED_START_X = MOTOR_STEPS_X; // Initial speed of a motor, steps / second.
const long ACCELERATION_X = 10 * MOTOR_STEPS_X; // Acceleration of a motor, steps / second ^ 2.
const long SPEED_MANUAL_MOVE_X = 3 * MOTOR_STEPS_X; // Maximum speed of a motor during manual move, steps / second.
const bool INVERT_X = true; // change (true/false) if the carriage moves e.g. "left" when you press "right".
const bool NEEDS_REST_X = false; // Set to false for all kinds of drivers or X will be unlocked when not moving.
const long MAX_TRAVEL_MM_X = 250; // Cross slide doesn't allow to travel more than this in one go, 25cm
//const long BACKLASH_DU_X = 2000; // 0.20mm backlash in deci-microns (10^-7 of a meter)
const char NAME_X = 'X'; // Text shown on screen before axis position value, GCode axis name

// Manual stepping with left/right/up/down buttons. Only used when step isn't default continuous (1mm or 0.1").
const long STEP_TIME_MS = 500; // Time in milliseconds it should take to make 1 manual step.
const long DELAY_BETWEEN_STEPS_MS = 80; // Time in milliseconds to wait between steps.

/* Changing anything below shouldn't be needed for basic use. */

// Configuration for axis connected to A1. This is uncommon. Dividing head (C) motor parameters.
// Throughout the configuration below we assume 1mm = 1degree of rotation, so 1du = 0.0001degree.
const bool ACTIVE_A1 = false; // Whether the axis is connected
const bool ROTARY_A1 = true; // Whether the axis is rotary or linear
const long MOTOR_STEPS_A1 = 300; // Number of motor steps for 1 rotation of the the worm gear screw (full step with 20:30 reduction)
const long SCREW_A1_DU = 20000; // Degrees multiplied by 10000 that the spindle travels per 1 turn of the worm gear. 2 degrees.
const long SPEED_START_A1 = 1600; // Initial speed of a motor, steps / second.
const long ACCELERATION_A1 = 16000; // Acceleration of a motor, steps / second ^ 2.
const long SPEED_MANUAL_MOVE_A1 = 3200; // Maximum speed of a motor during manual move, steps / second.
const bool INVERT_A1 = false; // change (true/false) if the carriage moves e.g. "left" when you press "right".
const bool NEEDS_REST_A1 = false; // Set to false for closed-loop drivers. Open-loop: true if you need holding torque, false otherwise.
const long MAX_TRAVEL_MM_A1 = 360; // Probably doesn't make sense to ask the dividin head to travel multiple turns.
const long BACKLASH_DU_A1 = 0; // Assuming no backlash on the worm gear
const char NAME_A1 = 'C'; // Text shown on screen before axis position value, GCode axis name

// Manual handwheels on A1 and A2. Ignore if you don't have them installed.
const bool PULSE_1_USE = false; // Whether there's a pulse generator connected on A11-A13 to be used for movement.
const char PULSE_1_AXIS = NAME_Z; // Set to NAME_X to make A11-A13 pulse generator control X instead.
const bool PULSE_1_INVERT = false; // Set to true to change the direction in which encoder moves the axis
const bool PULSE_2_USE = false; // Whether there's a pulse generator connected on A21-A23 to be used for movement.
const char PULSE_2_AXIS = NAME_X; // Set to NAME_Z to make A21-A23 pulse generator control Z instead.
const bool PULSE_2_INVERT = true; // Set to false to change the direction in which encoder moves the axis
const float PULSE_PER_REVOLUTION = 100; // PPR of handwheels used on A1 and/or A2.
const long PULSE_MIN_WIDTH_US = 1000; // Microseconds width of the pulse that is required for it to be registered. Prevents noise.
const long PULSE_HALF_BACKLASH = 2; // Prevents spurious reverses when moving using a handwheel. Raise to 3 or 4 if they still happen.

const int ENCODER_STEPS_INT = ENCODER_PPR * 2; // Number of encoder impulses PCNT counts per revolution of the spindle
//const int ENCODER_FILTER = 2; // Encoder pulses shorter than this will be ignored. Clock cycles, 1 - 1023.
const int ENCODER_FILTER_NS = 25; // Encoder pulses shorter than this will be ignored. In ns ---> Todo, is this too short?
const int PCNT_LIM = 31000; // Limit used in hardware pulse counter logic.
const int PCNT_CLEAR = 30000; // Limit where we reset hardware pulse counter value to avoid overflow. Less than PCNT_LIM.
const long DUPR_MAX = 254000; // No more than 1 inch pitch
const int STARTS_MAX = 124; // No more than 124-start thread
const long PASSES_MAX = 999; // No more turn or face passes than this
const long SAFE_DISTANCE_DU = 5000; // Step back 0.5mm from the material when moving between cuts in automated modes
const long SAVE_DELAY_US = 5000000; // Wait 5s after last save and last change of saveable data before saving again
const long DIRECTION_SETUP_DELAY_US = 5; // Stepper driver needs some time to adjust to direction change
const long STEPPED_ENABLE_DELAY_MS = 100; // Delay after stepper is enabled and before issuing steps

// Version of the pref storage format, should be changed when non-backward-compatible
// changes are made to the storage logic, resulting in Preferences wipe on first start.
#define PREFERENCES_VERSION 1
#define PREF_NAMESPACE "h4"
#define GCODE_NAMESPACE "gc"

// GCode-related constants.
const float LINEAR_INTERPOLATION_PRECISION = 0.1; // 0 < x <= 1, smaller values make for quicker G0 and G1 moves
const long GCODE_WAIT_EPSILON_STEPS = 10;
const bool SPINDLE_PAUSES_GCODE = true; // pause GCode execution when spindle stops
const int GCODE_MIN_RPM = 30; // pause GCode execution if RPM is below this

// To be incremented whenever a measurable improvement is made.
#define SOFTWARE_VERSION 98

// To be changed whenever a different PCB / encoder / stepper / ... design is used.
#define HARDWARE_VERSION 4

#define Z_ENA 16
#define Z_DIR 17
#define Z_STEP 18

#define X_ENA 8
#define X_DIR 19
#define X_STEP 20

#define BUZZ 4
#define KEYS_SCL 5
#define KEYS_SDA 6

#define A11 9
#define A12 10
#define A13 11

#define A21 12
#define A22 13
#define A23 14

#ifdef DISPLAY_I2C_EXPANDER
// If using display with I2C expander, only two pins are used
#define DISP_SDA  2
#define DISP_SCL  1
#else
// Default standard display
#define DISP_RS 21
#define DISP_EN 48
#define DISP_D0 47
#define DISP_D1 38
#define DISP_D2 39
#define DISP_D3 40
#define DISP_D4 41
#define DISP_D5 42
#define DISP_D6 2
#define DISP_D7 1
#endif


#define B_LEFT 57
#define B_RIGHT 37
#define B_UP 47
#define B_DOWN 67
#define B_MINUS 5
#define B_PLUS 64
#define B_ON 17
#define B_OFF 27
#define B_STOPL 7
#define B_STOPR 15
#define B_STOPU 6
#define B_STOPD 16
#define B_DISPL 14
#define B_STEP 24
#define B_SETTINGS 34
#define B_MEASURE 54
#define B_REVERSE 44
#define B_0 51
#define B_1 41
#define B_2 61
#define B_3 31
#define B_4 2
#define B_5 21
#define B_6 12
#define B_7 11
#define B_8 22
#define B_9 1
#define B_BACKSPACE 32
#define B_MODE_GEARS 42
#define B_MODE_TURN 52
#define B_MODE_FACE 62
#define B_MODE_CONE 3
#define B_MODE_CUT 13
#define B_MODE_THREAD 23
#define B_MODE_OTHER 33
#define B_X 53
#define B_Z 43
#define B_A 4
#define B_B 63

#define PREF_VERSION "v"
#define PREF_DUPR "d"
#define PREF_POS_Z "zp"
#define PREF_LEFT_STOP_Z "zls"
#define PREF_RIGHT_STOP_Z "zrs"
#define PREF_ORIGIN_POS_Z "zpo"
#define PREF_POS_GLOBAL_Z "zpg"
#define PREF_MOTOR_POS_Z "zpm"
#define PREF_DISABLED_Z "zd"
#define PREF_POS_X "xp"
#define PREF_LEFT_STOP_X "xls"
#define PREF_RIGHT_STOP_X "xrs"
#define PREF_ORIGIN_POS_X "xpo"
#define PREF_POS_GLOBAL_X "xpg"
#define PREF_MOTOR_POS_X "xpm"
#define PREF_DISABLED_X "xd"
#define PREF_POS_A1 "a1p"
#define PREF_LEFT_STOP_A1 "a1ls"
#define PREF_RIGHT_STOP_A1 "a1rs"
#define PREF_ORIGIN_POS_A1 "a1po"
#define PREF_POS_GLOBAL_A1 "a1pg"
#define PREF_MOTOR_POS_A1 "a1pm"
#define PREF_DISABLED_A1 "a1d"
#define PREF_SPINDLE_POS "sp"
#define PREF_SPINDLE_POS_AVG "spa"
#define PREF_OUT_OF_SYNC "oos"
#define PREF_SPINDLE_POS_GLOBAL "spg"
#define PREF_SHOW_ANGLE "ang"
#define PREF_SHOW_TACHO "rpm"
#define PREF_STARTS "sta"
#define PREF_MODE "mod"
#define PREF_MEASURE "mea"
#define PREF_CONE_RATIO "cr"
#define PREF_TURN_PASSES "tp"
#define PREF_MOVE_STEP "ms"
#define PREF_AUX_FORWARD "af"
#define PREF_BACKLASH_Z "blz"
#define PREF_BACKLASH_X "blx"

#define MOVE_STEP_1 10000 // 1mm
#define MOVE_STEP_2 1000 // 0.1mm
#define MOVE_STEP_3 100 // 0.01mm

#define MOVE_STEP_IMP_1 25400 // 1/10"
#define MOVE_STEP_IMP_2 2540 // 1/100"
#define MOVE_STEP_IMP_3 254 // 1/1000" also known as 1 thou

#define MODE_NORMAL 0
#define MODE_ASYNC 2
#define MODE_CONE 3
#define MODE_TURN 4
#define MODE_FACE 5
#define MODE_CUT 6
#define MODE_THREAD 7
#define MODE_ELLIPSE 8
#define MODE_GCODE 9
#define MODE_A1 10

#define MEASURE_METRIC 0
#define MEASURE_INCH 1
#define MEASURE_TPI 2

#define ESTOP_NONE 0
#define ESTOP_KEY 1
#define ESTOP_POS 2
#define ESTOP_MARK_ORIGIN 3
#define ESTOP_ON_OFF 4
#define ESTOP_OFF_MANUAL_MOVE 5

// For MEASURE_TPI, round TPI to the nearest integer if it's within this range of it.
// E.g. 80.02tpi would be shown as 80tpi but 80.04tpi would be shown as-is.
const float TPI_ROUND_EPSILON = 0.03;

const float ENCODER_STEPS_FLOAT = ENCODER_STEPS_INT; // Convenience float version of ENCODER_STEPS_INT
const long RPM_BULK = ENCODER_STEPS_INT; // Measure RPM averaged over this number of encoder pulses
const long RPM_UPDATE_INTERVAL_MICROS = 1000000; // Don't redraw RPM more often than once per second

const long GCODE_FEED_DEFAULT_DU_SEC = 20000; // Default feed in du/sec in GCode mode
const float GCODE_FEED_MIN_DU_SEC = 167; // Minimum feed in du/sec in GCode mode - F1

#define DREAD(x) digitalRead(x)
#define DHIGH(x) digitalWrite(x, HIGH)
#define DLOW(x) digitalWrite(x, LOW)
#define DWRITE(x, y) digitalWrite(x, y)

#define DELAY(x) vTaskDelay(x / portTICK_PERIOD_MS);

// ESP32 hardware pulse counter library used to count spindle encoder pulses.
#include "driver/pulse_cnt.h"

#include <SPI.h>
#include <Wire.h>

TwoWire I2C_keys = TwoWire(0);

#ifdef DISPLAY_I2C_EXPANDER
  TwoWire I2C_disp = TwoWire(1);  // Generate a secondary I2C object
  #include "LiquidCrystal_I2C_pt.h"
  //I2C_disp.setPins(DISP_SDA, DISP_SCL);
  LiquidCrystal_I2C lcd(0x27,20,4, &I2C_disp);
#else
  #include <LiquidCrystal.h>
  LiquidCrystal lcd(DISP_RS, DISP_EN, DISP_D0, DISP_D1, DISP_D2, DISP_D3, DISP_D4, DISP_D5, DISP_D6, DISP_D7);
#endif

#define LCD_HASH_INITIAL -3845709 // Random number that's unlikely to naturally occur as an actual hash
long lcdHashLine0 = LCD_HASH_INITIAL;
long lcdHashLine1 = LCD_HASH_INITIAL;
long lcdHashLine2 = LCD_HASH_INITIAL;
long lcdHashLine3 = LCD_HASH_INITIAL;
bool splashScreen = false;

#include <Preferences.h>

#include <Adafruit_TCA8418.h>
Adafruit_TCA8418 keypad;
unsigned long keypadTimeUs = 0;

// Most buttons we only have "down" handling, holding them has no effect.
// Buttons with special "holding" logic have flags below.
bool buttonLeftPressed = false;
bool buttonRightPressed = false;
bool buttonUpPressed = false;
bool buttonDownPressed = false;
bool buttonOffPressed = false;
bool buttonGearsPressed = false;
bool buttonTurnPressed = false;

bool inNumpad = false;
int numpadDigits[20];
int numpadIndex = 0;

bool isOn = false;
bool nextIsOn; // isOn value that should be applied asap
bool nextIsOnFlag; // whether nextIsOn requires attention
unsigned long resetMillis = 0;
int emergencyStop = 0;

bool beepFlag = false; // allows time-critical code to ask for a beep on another core

long dupr = 0; // pitch, tenth of a micron per rotation
long savedDupr = 0; // dupr saved in Preferences
long nextDupr = dupr; // dupr value that should be applied asap
bool nextDuprFlag = false; // whether nextDupr requires attention

SemaphoreHandle_t motionMutex; // controls blocks of code where variables affecting the motion loop() are changed

int starts = 1; // number of starts in a multi-start thread
int savedStarts = 0; // starts saved in Preferences
int nextStarts = starts; // number of starts that should be used asap
bool nextStartsFlag = false; // whether nextStarts requires attention

struct Axis {
  SemaphoreHandle_t mutex;

  char name;
  bool active;
  bool rotational;
  float motorSteps; // motor steps per revolution of the axis
  float screwPitch; // lead screw pitch in deci-microns (10^-7 of a meter)

  long pos; // relative position of the tool in stepper motor steps
  long savedPos; // value saved in Preferences
  float fractionalPos; // fractional distance in steps that we meant to travel but couldn't
  long originPos; // relative position of the stepper motor to origin, in steps
  long savedOriginPos; // originPos saved in Preferences
  long posGlobal; // global position of the motor in steps
  long savedPosGlobal; // posGlobal saved in Preferences
  int pendingPos; // steps of the stepper motor that we should make as soon as possible
  long motorPos; // position of the motor in stepper motor steps, same as pos unless moving back, then differs by backlashSteps
  long savedMotorPos; // motorPos saved in Preferences
  bool continuous; // whether current movement is expected to continue until an unknown position

  long leftStop; // left stop value of pos
  long savedLeftStop; // value saved in Preferences
  long nextLeftStop; // left stop value that should be applied asap
  bool nextLeftStopFlag; // whether nextLeftStop required attention

  long rightStop; // right stop value of pos
  long savedRightStop; // value saved in Preferences
  long nextRightStop; // right stop value that should be applied asap
  bool nextRightStopFlag; // whether nextRightStop requires attention

  long speed; // motor speed in steps / second
  long speedStart; // Initial speed of a motor, steps / second.
  long speedMax; // To limit max speed e.g. for manual moves
  long speedManualMove; // Maximum speed of a motor during manual move, steps / second.
  long acceleration; // Acceleration of a motor, steps / second ^ 2.
  long decelerateSteps; // Number of steps before the end position the deceleration should start.

  bool direction; // To reset speed when direction changes.
  bool directionInitialized;
  unsigned long stepStartUs;
  int stepperEnableCounter;
  bool disabled;
  bool savedDisabled;

  bool invertStepper; // change (true/false) if the carriage moves e.g. "left" when you press "right".
  bool needsRest; // set to false for closed-loop drivers, true for open-loop.
  bool movingManually; // whether stepper is being moved by left/right buttons
  long estopSteps; // amount of steps to exceed machine limits
  long backlash;              //  backlash (long decimicrons)
  long savedBacklash;     //  backlash saved in pref (long decimicrons)
  long backlashSteps; // amount of steps in reverse direction to re-engage the carriage
  long gcodeRelativePos; // absolute position in steps that relative GCode refers to

  int ena; // Enable pin of this motor
  int dir; // Direction pin of this motor
  int step; // Step pin of this motor
};

long numpadBacklash;  //  backlash saved temporarly to wait for button release (long decimicrons)
pcnt_unit_handle_t pcnt_unit_1 = NULL;
pcnt_channel_handle_t pcnt_chan_1A = NULL;

void initAxis(Axis* a, char name, bool active, bool rotational, float motorSteps, float screwPitch, long speedStart, long speedManualMove,
    long acceleration, bool invertStepper, bool needsRest, long maxTravelMm, long backlashDu, int ena, int dir, int step) {
  a->mutex = xSemaphoreCreateMutex();

  a->name = name;
  a->active = active;
  a->rotational = rotational;
  a->motorSteps = motorSteps;
  a->screwPitch = screwPitch;

  a->pos = 0;
  a->savedPos = 0;
  a->fractionalPos = 0.0;
  a->originPos = 0;
  a->savedOriginPos = 0;
  a->posGlobal = 0;
  a->savedPosGlobal = 0;
  a->pendingPos = 0;
  a->motorPos = 0;
  a->savedMotorPos = 0;
  a->continuous = false;

  a->leftStop = 0;
  a->savedLeftStop = 0;
  a->nextLeftStopFlag = false;

  a->rightStop = 0;
  a->savedRightStop = 0;
  a->nextRightStopFlag = false;

  a->speed = speedStart;
  a->speedStart = speedStart;
  a->speedMax = LONG_MAX;
  a->speedManualMove = speedManualMove;
  a->acceleration = acceleration;
  a->decelerateSteps = 0;
  long s = speedManualMove;
  while (s > speedStart) {
    a->decelerateSteps++;
    s -= a->acceleration / float(s);
  }

  a->direction = true;
  a->directionInitialized = false;
  a->stepStartUs = 0;
  a->stepperEnableCounter = 0;
  a->disabled = false;
  a->savedDisabled = false;

  a->invertStepper = invertStepper;
  a->needsRest = needsRest;
  a->movingManually = false;
  a->estopSteps = maxTravelMm * 10000 / a->screwPitch * a->motorSteps;
  a->backlashSteps = backlashDu * a->motorSteps / a->screwPitch;
  a->gcodeRelativePos = 0;
  a->backlash = 0;           //  
  a->savedBacklash = 0;  //

  a->ena = ena;
  a->dir = dir;
  a->step = step;
}

void calculateBacklashSteps(Axis* a) {  //  calculate backlash in steps after reading pref or after modification
  a->backlashSteps = a->backlash * a->motorSteps / a->screwPitch;
}
Axis z;
Axis x;
Axis a1;

unsigned long saveTime = 0; // micros() of the previous Prefs write
unsigned long spindleEncTime = 0; // micros() of the previous spindle update
unsigned long spindleEncTimeDiffBulk = 0; // micros() between RPM_BULK spindle updates
unsigned long spindleEncTimeAtIndex0 = 0; // micros() when spindleEncTimeIndex was 0
int spindleEncTimeIndex = 0; // counter going between 0 and RPM_BULK - 1
long spindlePos = 0; // Spindle position
long spindlePosAvg = 0; // Spindle position accounting for encoder backlash
long savedSpindlePosAvg = 0; // spindlePosAvg saved in Preferences
long savedSpindlePos = 0; // spindlePos value saved in Preferences
int spindleCount = 0; // Last processed spindle encoder pulse counter value.
int spindlePosSync = 0; // Non-zero if gearbox is on and a soft limit was removed while axis was on it
int savedSpindlePosSync = 0; // spindlePosSync saved in Preferences
long spindlePosGlobal = 0; // global spindle position that is unaffected by e.g. zeroing
long savedSpindlePosGlobal = 0; // spindlePosGlobal saved in Preferences

volatile int pulse1Delta = 0; // Outstanding pulses generated by pulse generator on terminal A1.
volatile int pulse2Delta = 0; // Outstanding pulses generated by pulse generator on terminal A2.

bool showAngle = false; // Whether to show 0-359 spindle angle on screen
bool showTacho = false; // Whether to show spindle RPM on screen
bool savedShowAngle = false; // showAngle value saved in Preferences
bool savedShowTacho = false; // showTacho value saved in Preferences
int shownRpm = 0;
unsigned long shownRpmTime = 0; // micros() when shownRpm was set

long moveStep = 0; // thousandth of a mm
long savedMoveStep = 0; // moveStep saved in Preferences

volatile int mode = -1; // mode of operation (ELS, multi-start ELS, asynchronous)
int nextMode = 0; // mode value that should be applied asap
bool nextModeFlag = false; // whether nextMode needs attention
int savedMode = -1; // mode saved in Preferences

int measure = MEASURE_METRIC; // Whether to show distances in inches
int savedMeasure = MEASURE_METRIC; // measure value saved in Preferences

float coneRatio = 1; // In cone mode, how much X moves for 1 step of Z
float savedConeRatio = 0; // value of coneRatio saved in Preferences
float nextConeRatio = 0; // coneRatio that should be applied asap
bool nextConeRatioFlag = false; // whether nextConeRatio requires attention

int turnPasses = 3; // In turn mode, how many turn passes to make
int savedTurnPasses = 0; // value of turnPasses saved in Preferences
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
void loop() {
  if (emergencyStop != ESTOP_NONE) {
    return;
  }
  if (xSemaphoreTake(motionMutex, 1) != pdTRUE) {
    return;
  }
  applySettings();
  processSpindleCounter();
  discountFullSpindleTurns();
  if (!isOn || dupr == 0 || spindlePosSync != 0) {
    // None of the modes work.
  } else if (mode == MODE_NORMAL) {
    modeGearbox();
  } else if (mode == MODE_TURN) {
    modeTurn(&z, &x);
  } else if (mode == MODE_FACE) {
    modeTurn(&x, &z);
  } else if (mode == MODE_CUT) {
    modeCut();
  } else if (mode == MODE_CONE) {
    modeCone();
  } else if (mode == MODE_THREAD) {
    modeTurn(&z, &x);
  } else if (mode == MODE_ELLIPSE) {
    modeEllipse(&z, &x);
  }
  moveAxis(&z);
  moveAxis(&x);
  if (ACTIVE_A1) moveAxis(&a1);
  xSemaphoreGive(motionMutex);
}

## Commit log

2024-05-05 - Added KiCad files
    [NanoElsH4.kicad_pcb, NanoElsH4.kicad_sch, NanoElsH4Keypad.kicad_pcb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]
2024-05-05 - moved files
    [NanoElsH4revised1.kicad_pcb, NanoElsH4revised1.kicad_sch]
2024-06-24 update (ESP32 lib): Update of ESP32 component in Arduino Upgrade to Espressive ESP32 3.0.1 boards package (based on ESP-IDF v5.1.4). Therefore "pulse counter" and "hardware timer" rewritten.
    feat (display): Display in I2C mode
    Added possibility for display in I2C mode for displays with I2C backpack (e.g. PCF8574). Seems currently working faultless together with secondary I2C channel for keypad interface. Added LiquidCrysta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
    test: State of testing incomplete
    Currently not completely tested, but encoder detects something. Hardware timer for ASYNC and A1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
2024-06-24 - Added actual KiCad 8 files (layout ready, but some cosmetic documentation ToDo's)
    [NanoElsH4revised1.kicad_pcb, NanoElsH4revised1.kicad_sch, NanoElsH4revised1_IO_v1.kicad_sch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]
2025-04-05 - KiCad 9...
    [NanoElsH4revised1.kicad_pcb, NanoElsH4revised1.kicad_sch, NanoElsH4revised1_IO_v1.kicad_sch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]
2025-04-05 - activated I2C display - Cahnged lathe parameters - Changed binary define prefix
2025-04-06 - Added suggested code for backslash and show limit values. (Discussion issue #301 and issue #242) - Tested backslash settings via dial gauge and after power reset. Seems to be OK, including the sett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
    [h4.ino]
